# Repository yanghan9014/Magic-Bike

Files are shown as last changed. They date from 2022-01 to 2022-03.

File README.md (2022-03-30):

# Magic Bike (a spooky bike that could stalk you)
Embedded System Final Report  -- By 楊學翰 B08901054 陳韋旭 B08901181
---

## Introduction & Motivation
We originally intend to build a self-balancing & self-navigating bike just like the XUAN-Bike (https://github.com/peng-zhihui/XUAN), but found self-balancing far too difficult. We then shift our focus solely onto self-navigating.

In this project we established the pipeline of RGBD image processing and Jetson Nano-STM32 communication. Although we couldn't complete self-navigation in time, we demonstrated our work by making our bike follow a person (wearing red, for now).



## Method
### Development boards & motors
- STM32L4
- Jetson Nano
- RealSense depth camera D435
- 45kg-cm PWM controlled servo motor (Fashion Star HP8-A45) * 2
- Electric bike motor

### Hardware installation
We make use of 3D printers and laser cutter to make various kind of mounts
- Install electric motor on the back wheel
- Weld training wheels onto the bike frame
- Handlebar control:  servo motor + belt
- Brake control: servo motor + spool
- Attach RealSense camera



### How To Track A Person
- Version 1 – Track the person in red
   1. Take a color image and convert RGB into HSV
      ```
      boundaries = {
        "R": ([170, 80, 10], [180, 255, 255]), ... }
      bd = boundaries[color]
      img = msg_retriever.func_data['colorStream']['data']
      HSV_img = cv2.cvtColor(img, cv2.COLOR_RGB2HSV)

      mask = cv2.inRange(HSV_img, bd[0], bd[1])
      kernel = cv2.getStructuringElement(cv2.MORPH_RECT, (3,3))
      mask = cv2.morphologyEx(mask, cv2.MORPH_CLOSE, kernel, iterations=2)
      ```
   2. Create a mask of the red areas; calculate the average x coordinate of the mask
   3. The Horizontal Field of View(HFOV) is ≈69°; we can calculate ∆θ = arctan(∆x / (320 * cot(HFOV / 2)))
   4. Adjust the handlebar servo motor angle accordingly

- Version 2 - Track the closest person to the bike (not complete yet)
   - Employ YOLO v5 and get the bounding box coordinates of the closest person
   - We got YOLO v5 working on COLAB, but failed to install PyTorch with CUDA support on Jetson Nano
   - Once installation issues got resolved, version 2 would only require a minor fix

### How To Avoid Collision
- Get distance image from depth camera
- Crop out bottom ⅓ of the image (the floor is too close)
- Calculate the total area in which the distance < 1000m
- If the area reaches a certain threshold (5% of the full image), hold brake and cut off back wheel motor power

(We don't simply measure the closest distance to avoid false alarms)

### Power System


### Control System


### ROS2 (on Jetson Nano)
Handle software communication between nodes
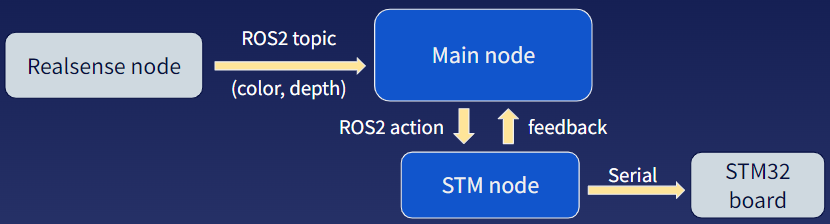
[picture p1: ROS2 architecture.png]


### Implemented techniques (from Embedded System course)
- Docker
- WiFi AP
- Multithreading
- PWM control
- Serial communication
- Streaming with GStreamer

#### Docker
- Solve dependency and installation issues
- Used ROS2 docker image from docker hub (https://hub.docker.com/r/osrf/ros2/)
- Enable auto-restart of docker container

#### WiFi AP
- Internet IP changes when Jetson Nano connects to a different network
- Solution: Make Jetson Nano a WiFi AP

#### Multithreading
- Collision avoidance & camera should be constantly on
- Camera
   - Camera input is divided into color and depth
   - Need two subscribers on two seperate threads
   ```
   executor.add_node(msg_retriever)
   executor_thread = threading.Thread(target=msg_retriever.wait_for_messages, daemon=True, args = (themes, executor))
   executor_thread.start()
   ```
- Collision avoidance
   - Create a separate thread to constantly monitor obstacles ahead of the bike
   ```
   col = threading.Thread(target = collision_avoidance)
   ...
   col.start()
   stalk()
   ...
   col.join()
   ```

#### PWM Control
- Use 50 Hz PWM to control Servo (duty cycle: 10%~20%)
- Use 50 kHZ PWM & low-pass filter to simulate DAC
   - Throttle signal: 0.8V ~ 3.6V DC
   - STM32 can only output digital signals or PWM

#### Serial Communication
- Between Jetson Nano & STM32
- Divide the tasks
   - STM32 is a real-time OS. Handles PWM timer to control servo motor
   - Jetson Nano has built-in GPU. Can accelerate image processing speed and provide streaming
   ```
   self.serial_port = serial.Serial(
      port="/dev/ttyACM0",
      baudrate=9600,
      timeout=0.5
   )
   ...
   self.serial_port.write(sendMessage.encode('ascii'))
   ```

#### GStreamer (not finished yet)
- We've successfully streamed with Pi Camera

```gst-launch-1.0   nvarguscamerasrc !       "video/x-raw(memory:NVMM), width=1920, height=1080, framerate=30/1" !   nvvidconv flip-method=2 !    omxh264enc control-rate=2 bitrate=4000000 !      "video/x-h264, stream-format=byte-stream" !   rtph264pay mtu=1400 !    udpsink host=192.168.10.110 port=5000 sync=false async=false```
- But failed with RealSense
   - Realsense src is not fully supported on GStreamer yet

## Problems & solutions
1. No analog DC signal on STM32 board
Analog DC signal (0.8V ~ 3.6V DC) is required to control the throttle, which is not supported on STM32 GPIOs
   - Solution:
      - Use PWM & RC low-pass filter to simulate analog voltage signal
2. RealSense camera delay
Cmera input always comes with some delay
   - Solution: 
      - Slow down bike speed
      - Add delay between each "turn left" or "turn right" command
3. Jetson Nano's IP changes everytime it connected to a different WiFi
   - Solution:
      - Make Jetson Nano itself a WiFi AP 

## Result & demo
Demo video link: https://www.youtube.com/watch?v=ACSJ1eG-BSU

<a href="http://www.youtube.com/watch?feature=player_embedded&v=ACSJ1eG-BSU
" target="_blank"><img src="http://img.youtube.com/vi/ACSJ1eG-BSU/0.jpg" 
alt="IMAGE ALT TEXT HERE" width="1200" height="900" border="10" /></a>

## Future Prospects
This project is an unfortunate simplification of an overly ambitious idea.
Having figured out how to utilize the depth camera, we established a foundation that we can easily build upon.
After this, we plan to...
1. Detect and avoid (or follow) certain objects (cars, people, animals...) on the road with YOLO v5.
2. Detect road edges (https://github.com/amusi/awesome-lane-detection), and apply projective transform to get a bird's-eye-view. Auto-correct bike direction if not parellel to the road.
3. Install GPS module and connect with path-finding API
4. Figure out an algorithm and complete fully automated navigation.

## Reference
- Xuan bike github: https://github.com/peng-zhihui/XUAN
- Xuan bike YouTube: https://www.youtube.com/watch?v=kCL2d7wZjU8&t=507s&ab_channel=%E7%A8%9A%E6%99%96%E5%90%9B
- ROS2 tutorial: https://docs.ros.org/en/foxy/Tutorials.html
- Road edge detection: https://github.com/amusi/awesome-lane-detection

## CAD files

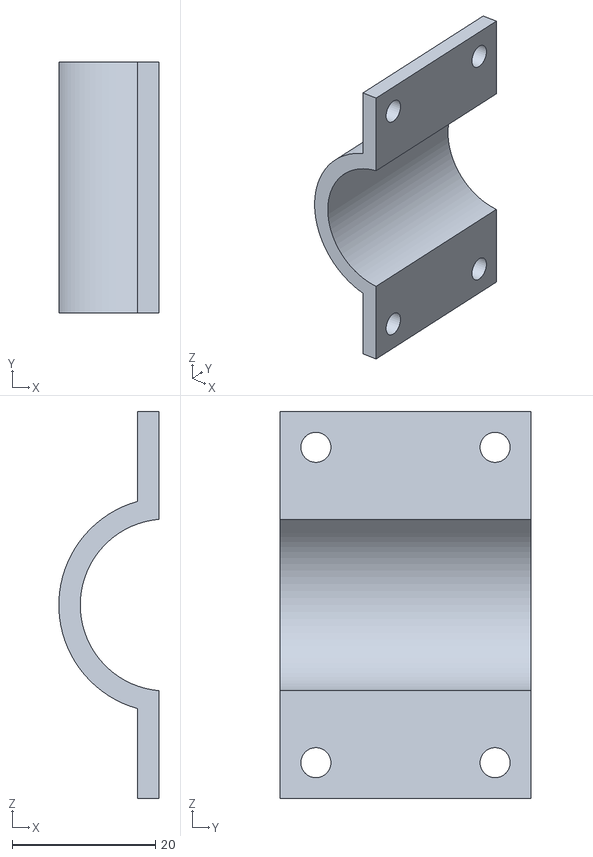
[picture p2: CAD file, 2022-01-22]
cad/煞車Servo夾.stl
14.0 x 35.0 x 54.0

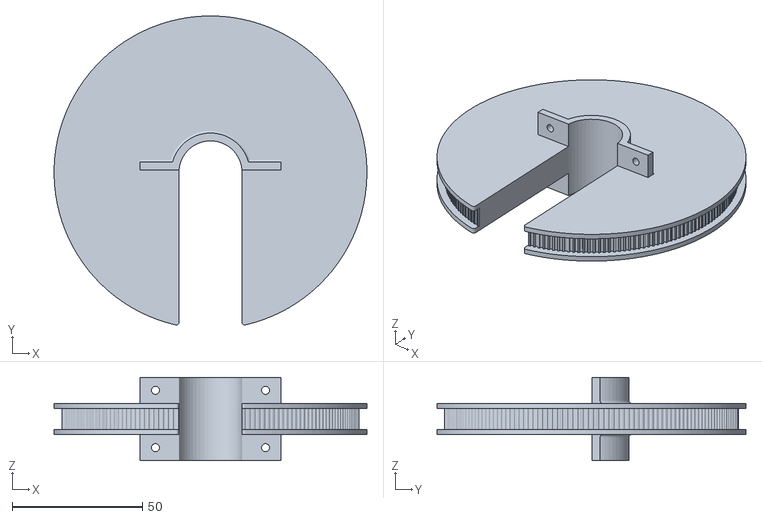
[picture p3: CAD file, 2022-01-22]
cad/龍頭同步輪.stl
120.0 x 118.5 x 32.0

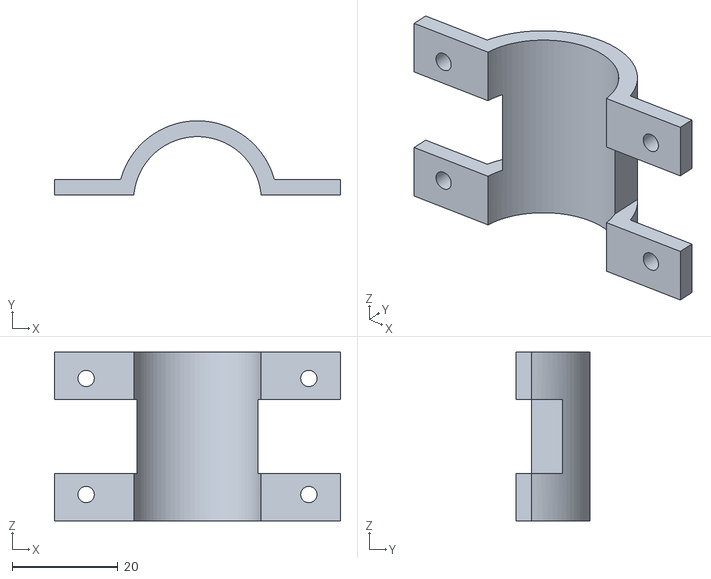
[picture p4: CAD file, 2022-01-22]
cad/龍頭同步輪固定夾件.stl
54.2 x 14.1 x 32.0

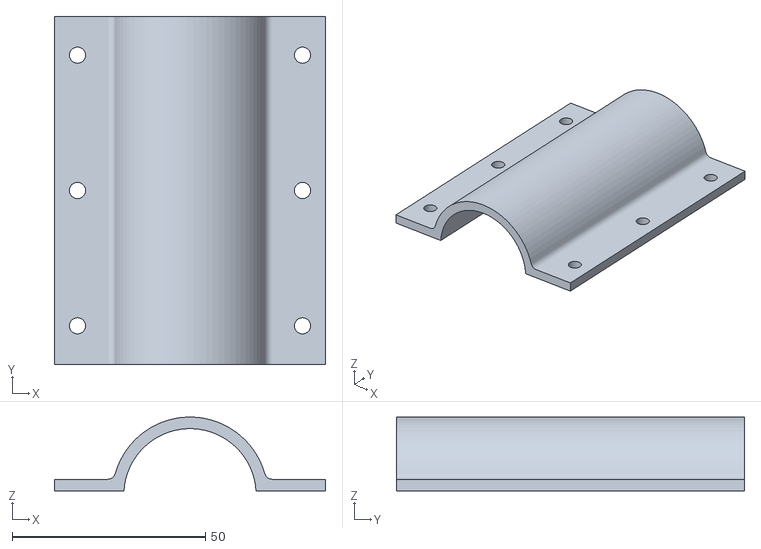
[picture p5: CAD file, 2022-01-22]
cad/龍頭Servo固定夾.stl
70.2 x 90.0 x 19.1

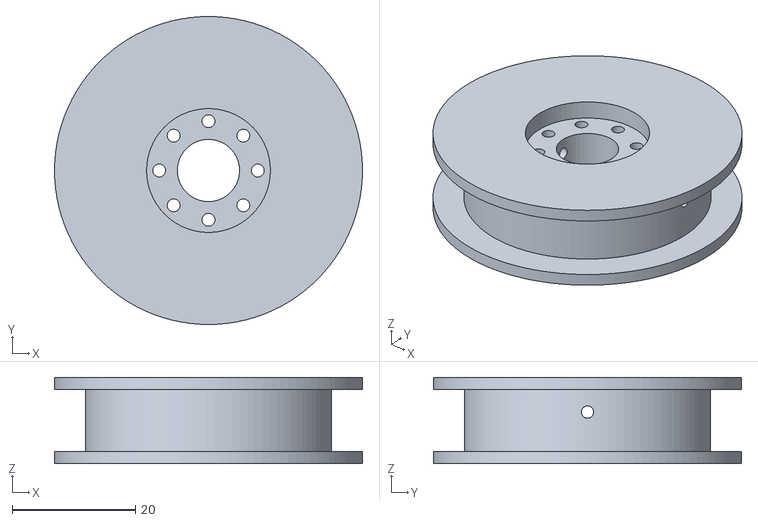
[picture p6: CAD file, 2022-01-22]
cad/煞車Servo捲線器.stl
50.0 x 50.0 x 14.0

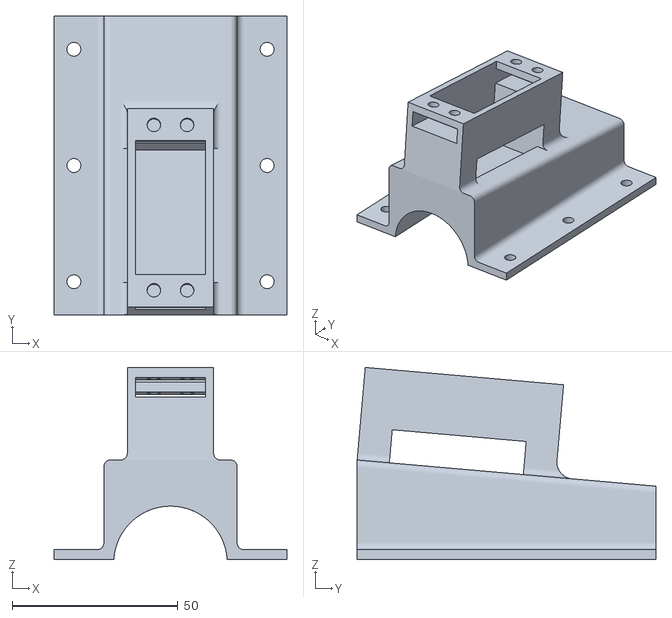
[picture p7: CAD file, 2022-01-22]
cad/龍頭Servo固定座.stl
70.2 x 90.0 x 57.9

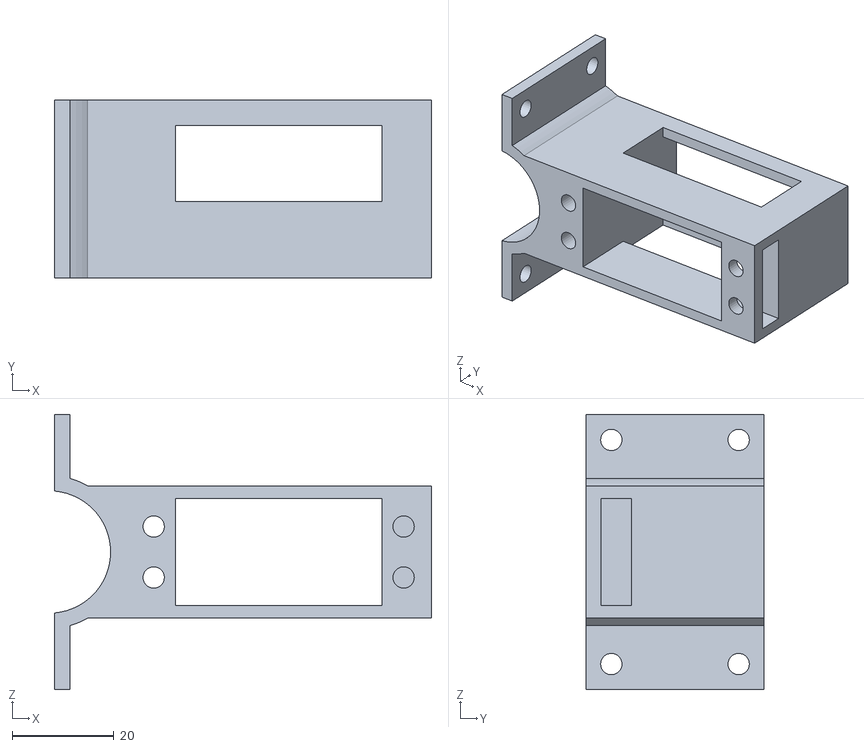
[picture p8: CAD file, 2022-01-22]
cad/煞車Servo座.stl
74.0 x 35.0 x 54.0

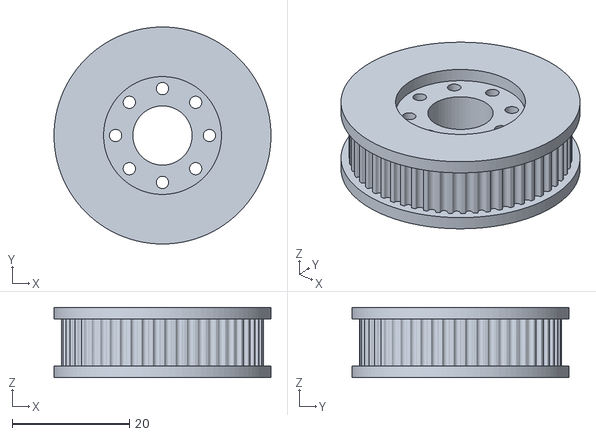
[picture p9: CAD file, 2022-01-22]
cad/伺服馬達同步輪.stl
37.0 x 37.0 x 12.0

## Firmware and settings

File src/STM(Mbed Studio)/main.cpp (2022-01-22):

#include "PeripheralNames.h"
#include "PinNames.h"
#include "PwmOut.h"
#include "mbed.h"
#include "mbed_wait_api.h"
#include <cstdio>



PwmOut pedal(D3);
PwmOut direction(D4);
PwmOut brake(D5);

float nowSpeed;
const float speedDelta = 0.02;
const int speedWait = 100000;

const float servoLow = 0.02;   // 2%
const float servoHigh = 0.128; // 12.8%
const float servoDelta = 0.001; //0.1%

const float leftDir = servoHigh;//servoLow + (servoHigh - servoLow) * 0.25;
const float rightDir = servoLow;//servoLow + (servoHigh - servoLow) * 0.75;
const float midDir = (servoLow + servoHigh) / 2;
float nowDir;

bool nowStop;

void setup() {
    pedal.period(0.00002); // 50 kHz
    direction.period(0.02f); // 50 Hz
    brake.period(0.02f);

    nowSpeed = 0;
    nowDir = midDir;
    nowStop = false;
}
float calculateDuty(float speed) {
    float min = 0.3;  // 20%
    float max = 1;
    return min + (max-min) * speed;
}
void run(float speed) { //speed 0~1
    if (speed > 1)
        speed = 1;
    if (speed < 0)
        speed = 0;
    if (speed > nowSpeed) {
        while (speed > nowSpeed) {
            nowSpeed += speedDelta;
            pedal.write(calculateDuty(nowSpeed));
            wait_us(speedWait);
        }
        nowSpeed = speed;
        pedal.write(calculateDuty(nowSpeed));
    }
    else {
        while (speed < nowSpeed) {
            nowSpeed -= speedDelta;
            pedal.write(calculateDuty(nowSpeed));
            wait_us(speedWait);
        }
        nowSpeed = speed;
        pedal.write(calculateDuty(nowSpeed));
    }
}

float turnTrans(int t) {
    return (t/90.0f) * 0.054f;
}

void turnLeftDelta(float delta) {
    int count = delta / servoDelta;
    for (int i = 0; i < count; ++i) {
        nowDir += servoDelta;
        direction.write(nowDir);
        wait_us(20000);
        if (nowDir > leftDir) {
            nowDir = leftDir;
            direction.write(nowDir);
            break;
        }
    }
}


void turnRightDelta(float delta) {
    int count = delta / servoDelta;
    for (int i = 0; i < count; ++i) {
        nowDir -= servoDelta;
        direction.write(nowDir);
        wait_us(20000);
        if (nowDir < rightDir) {
            nowDir = rightDir;
            direction.write(nowDir);
            break;
        }
    }
}


void turnRight() {
    while (nowDir > rightDir) {
        nowDir -= servoDelta;
        direction.write(nowDir);
        wait_us(20000); // wait 50 ms
    }
    nowDir = rightDir;
    direction.write(nowDir);
}

void turnLeft() {
    while (nowDir < leftDir) {
        nowDir += servoDelta;
        direction.write(nowDir);
        wait_us(20000); // wait 50 ms
    }
    nowDir = leftDir;
    direction.write(nowDir);
}

void turnFront() {
    if (nowDir < midDir) {
        while (nowDir < midDir) {
            nowDir += servoDelta;
            direction.write(nowDir);
            wait_us(20000);
        }
    }
    else {
        while (nowDir > midDir) {
            nowDir -= servoDelta;
            direction.write(nowDir);
            wait_us(20000);
        }
    }
    nowDir = midDir;
    direction.write(nowDir);
}

void holdBrake() {
    if (nowStop)
        return;
    float output = servoHigh;
    while (output > servoLow) {
        brake.write(output);
        output -= servoDelta;
        wait_us(10000); //wait 100ms
    }
    nowStop = true;
}

void releaseBrake() {
    if (!nowStop)
        return;
    float output = servoLow;
    while (output < servoHigh) {
        brake.write(output);
        output += servoDelta;
        wait_us(10000); //wait 100ms
    }
    nowStop = false;
}
void waitSec(int us) {
    wait_us(1000000 * us);
}

// main() runs in its own thread in the OS
int main()
{
    DigitalOut led(LED1);
    led = false;
    setup();
    printf("set up finish\n");
    led = true;
    holdBrake();
    printf("DDDDD\n");
    turnFront();
    run(0.39);
    char c[50];
    while (1) {
        scanf("%s", c);
        int t = 0;
        for (int i = 0; c[i] != '\0'; ++i)
            t++;
        printf("I get message: %s\n", c);
        printf("msg len(expect 4, other will be ignore): %d\n", t);
        if (t != 4)
            continue;
        led = !led;
        if (c[0] == 'w') {
            run(0.39);
        }
        else if (c[0] == 's') {
            if (c[3] == '1') {  // s001 for hold
                holdBrake();
            }
            else {              // s000 for release
                releaseBrake();
            }
        }
        else if (c[0] == 'a') {
            turnLeft();
        }
        else if (c[0] == 'd') {
            turnRight();
        }
        else if (c[0] == 'f') {
            turnFront();
        }
        else if (c[0] == 'q') {
            int dir = (c[2] - '0') * 10 + (c[3] - '0');
            turnLeftDelta(turnTrans(dir));
        }
        else if (c[0] == 'e') {
            int dir = (c[2] - '0') * 10 + (c[3] - '0');
            turnRightDelta(turnTrans(dir));
        }
        else {
            printf("Error: get unknow command\n");
        }
        fflush(stdin);
    }
    run(0);
}

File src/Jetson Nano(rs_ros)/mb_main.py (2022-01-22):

import sys
import time
import rclpy
from rclpy.node import Node
from rclpy import qos
from sensor_msgs.msg import Image as msg_Image
from sensor_msgs.msg import Imu as msg_Imu
import numpy as np
import inspect
import ctypes
import struct
import os
import threading
#import matplotlib
#import matplotlib.pyplot as plt
import cv2
from rclpy.executors import MultiThreadedExecutor

from rs_ros.rs_listener import CWaitForMessage
from rs_ros.stm_action import MainActionClient
# from rs_ros.yolov5.inference import detect
# import torch
#from rs_ros.lane_detection_wrapper import *
# from rs_ros.find_color_center import color_center_dist

if (os.getenv('ROS_DISTRO') != "dashing"):
    import tf2_ros

def main():
    rclpy.init()
    executor = MultiThreadedExecutor()
    lock = threading.Lock()

    # model = torch.hub.load('ultralytics/yolov5', 'yolov5s')

    print("Try to listen")
    msg_params = {}
    themes = ['alignedDepthColor', 'colorStream']
    msg_retriever = CWaitForMessage(lock, themes, msg_params)
    time.sleep(3.0)

    executor.add_node(msg_retriever)
    executor_thread = threading.Thread(target=msg_retriever.wait_for_messages, daemon=True, args = (themes, executor))
    executor_thread.start()

    action_client = MainActionClient()
    print("=======================")
    print(" Activate! ")
    print("=======================")
    activate(msg_retriever, action_client)
    action_client.destroy_node()

    #=== Terminating... ===
    executor_thread.join()

def activate(msg_retriever, action_client):

    #net = parsingNet(pretrained = True).cuda() # we dont need auxiliary segmentation in testing
    #state_dict = torch.load('culane_18.pth', map_location = 'cpu')['model']
    #compatible_state_dict = {}
    #for k, v in state_dict.items():
    #    if 'module.' in k:
    #        compatible_state_dict[k[7:]] = v
    #    else:
    #        compatible_state_dict[k] = v

    #net.load_state_dict(compatible_state_dict, strict = False)

    def move(cmd):
        try:
            action_client.send_goal( cmd )
            rclpy.spin_once(action_client)
            time.sleep(0.7)
        except RuntimeError as e:
            print(e)

    def magic_init():
        print("=======================")
        print("Init bike position")
        print("=======================")
        # move("s001")
        # move("f000")
        time.sleep(2.0)
        move("w020")
        time.sleep(1.0)
        move("s000")
        print("fin")

    def turn(degree):
        if degree >= 0:
            move('e0' + str(abs(degree)).zfill(2))
        else:
            move('q0' + str(abs(degree)).zfill(2))
    def right90():
        stop()
        walk()
        turn(30)
        time.sleep(2.0)
        turn(0)

    def left90():
        stop()
        walk()
        turn(-30)
        time.sleep(2.0)
        turn(0)

    def too_close_ratio(dist_thresh=1200):
        try:
            #if not msg_retriever.depth_failed:
                dep = msg_retriever.func_data['alignedDepthColor']['data']
                dist_map = np.where(dep[:300, :] < dist_thresh, 1, 0)
                too_close_area = dist_map.sum()
                # print(too_close_area*1.0/(640*480), end=' ')
                return too_close_area * 1.0 / (640*480)
        except Exception as e:
            print("Error:", e)
            return 1.0

    def collision_avoidance(too_close_ratio_thresh = 0.1):
        brake = True
        while(True):
            if(too_close_ratio() > too_close_ratio_thresh):
                if not brake:
                    brake = True
                    print("too close! Braking...")
                    move('s001')
                    time.sleep(2.0)
            elif brake:
                brake = False
                print("Releasing brake")
                move('s000')


    def lane_detection():
        print(msg_retriever.func_data['colorStream'].keys())
        c_img = msg_retriever.func_data['colorStream']['data']
        #c_img = c_img.cuda()
        #with torch.no_grad():
        #    out = net(c_img)
        #if len(out) == 2:
        #    out, seg_out = out

        #t = time.localtime()
        #timestamp = time.strftime("%H:%M:%S", t)

        #generate_lines(out,c_img.shape, names=timestamp, localization_type = 'rel', flip_updown = True)


    def stalk(color = 'R'):
      print("=======================")
      print(" Start slaking color", color)
      print("=======================")
        
      
      while(True):
        #    c_img = msg_retriever.func_data['colorStream']['data']
        #    results = model(c_img)
        #    results = results.pandas().xyxy[0].to_dict()
        #    if 'person' in results['name'].values():
        #        print("Person detected")
        boundaries = {
        "R": ([170, 80, 10], [180, 255, 255]),
        "r": ([0, 100, 50], [3, 255, 255]),
        "G": ([53, 80, 50], [77, 255, 255]),
        "B": ([100, 100, 50], [112, 255, 255]),
        "Y": ([6, 100, 50], [20, 255, 255]),
        "K": ([0, 0, 0], [180, 255, 30]),
        "W": ([0, 0, 200], [180, 255, 255])
        }
        bd = boundaries[color]
        bd = np.array(bd, dtype='uint8')

        img = msg_retriever.func_data['colorStream']['data']
        HSV_img = cv2.cvtColor(img, cv2.COLOR_RGB2HSV)

        mask = cv2.inRange(HSV_img, bd[0], bd[1])
        kernel = cv2.getStructuringElement(cv2.MORPH_RECT, (3,3))
        mask = cv2.morphologyEx(mask, cv2.MORPH_CLOSE, kernel, iterations=2)

        tot = np.sum(mask)

        avg_m = np.sum(mask, axis=1)
        avg_n = np.sum(mask, axis=0)

        index_m = np.arange(mask.shape[0])
        index_n = np.arange(mask.shape[1])

        try:
            cen_coords = np.array( [round( np.dot(avg_m, index_m) / tot ), round( np.dot(avg_n, index_n) / tot )], dtype='int32')
            # print("x coords: ", cen_coords[1])

        # depth_img = msg_retriever.func_data['alignedDepthColor']['data']
        # color_dep = np.where(mask != 0, depth_img, 0)
        # color_dep = round( np.sum(color_dep)*255 / tot )
        # color_dep = min(50, color_dep)
        # print("Avg color ", color, " depth:", color_dep)
            delta_angle = np.arctan((cen_coords[1] - 320)*0.8 / 320) * 180. / np.pi
            delta_angle = round(delta_angle)
            delta_angle = max(delta_angle, -90)
            delta_angle = min(delta_angle, 90)
            turn( delta_angle )
            time.sleep(1.0)
        except Exception as e:
            # print(e)
            print("No ", color, " found", end=' ')
            pass

    lock = threading.Lock()
    col = threading.Thread(target = collision_avoidance)
    # sta = threading.Thread(target = stalk)

    # sta.start()
    magic_init()

    col.start()
    move("w020")
    stalk()

    #lane_detection()

    col.join()
    # sta.join()

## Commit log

2022-01-22 add cad & update README
    [伺服馬達同步輪.stl, 煞車Servo夾.stl, 煞車Servo座.stl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]
2022-01-22 readme & add src/STM32
